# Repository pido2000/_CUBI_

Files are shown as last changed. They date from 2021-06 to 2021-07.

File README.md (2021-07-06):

### Description

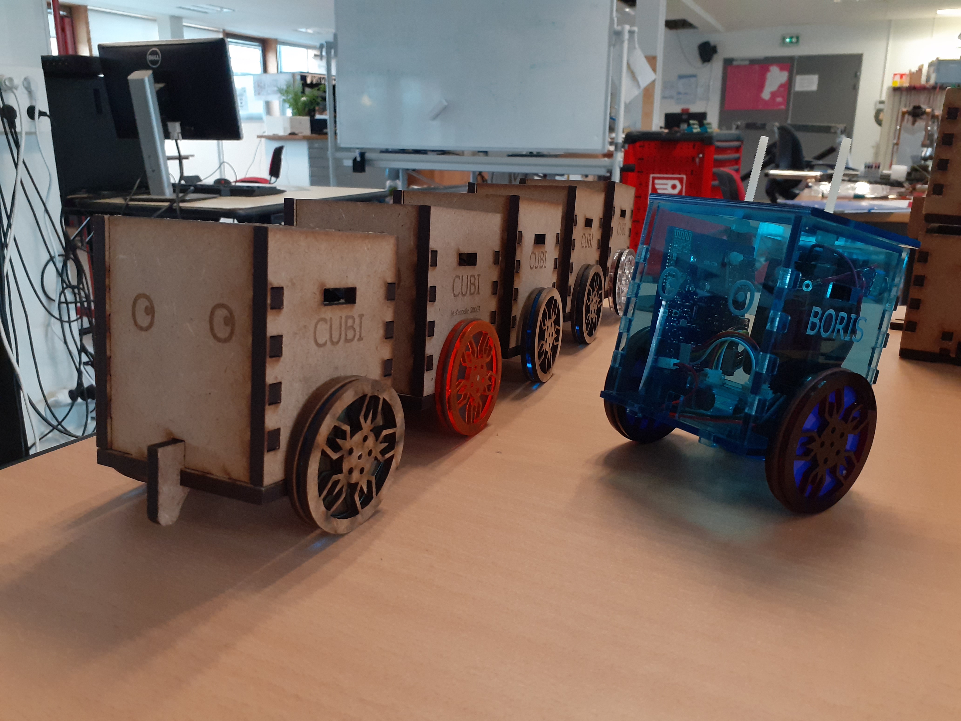
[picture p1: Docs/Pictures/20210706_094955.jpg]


Simple open source bluetooth controlled wheeled robot. Mechanical design, electronics and software designs available on this repo.
Remy F. used @Gregwar's Holo as a starting point.

The initial design is a cube like robot :

https://www.youtube.com/watch?v=2ZDV0_4vD0g

https://www.youtube.com/watch?v=TOusHRbKWQg

A second design was also made to play around cart-poling:

https://www.youtube.com/watch?v=Ubej95gH9Gs

TODO:

- Add Julien's O. designs and events

- Add Julien's A. and Jérémy's designs and event (cap science)

### Simulation
Some simulation stuff (simple kinematic control, inverted pendulum tests) is available in Python here :
https://bitbucket.org/RemiFabre/cubi/src/master/simulation/

0) Installation
You'll need Python (any version should work) and pygame
```
pip install pygame
```

1) Simple control of a wheeled robot (click around)
```
python main.py
```
https://www.youtube.com/watch?v=O8ZoUAvGYmE

2) Inverted pendulum (cart-pole) simulation
```
python cart_pole.py
```
https://www.youtube.com/watch?v=xhEcLnnj7fg

### How to make it work
You'll have to install the arm cross-compilation tools. On debian-like distributions,
you can get it with:

```
    sudo aptitude install build-essential git-core dfu-util openocd python \
        python-serial binutils-arm-none-eabi gcc-arm-none-eabi libstdc++-arm-none-eabi-newlib
```
If you're running an Ubuntu 14.04 or older, you might need to install the libstdc++-arm-none-eabi-newlib packet by hand. Download link :
http://ftp.de.debian.org/debian/pool/main/libs/libstdc++-arm-none-eabi/libstdc++-arm-none-eabi-newlib_4.8.3-9+4_all.deb

Command (if a conflict rises, you can add --force-overwrite to the following line):
```
	sudo dpkg -i libstdc++-arm-none-eabi-newlib_4.8.3-9+4_all.deb
```
Go to the `firmware/src` directory and edit the `Makefile` to set the appropriate
`BOARD` variable, targetting your servo.

You can then run:

```
make
```

Use an USB cable to connect your pc with the robot's board

```
make install
```
### Bluetooth

First you need to set the name and the pasword using a cable.

```
cu -l /dev/ttyACM0
btconf <name> <pswrd>
```

Then, you can control the robot without the need of a cable. The most straight-forward way is to download the "Metabot" app from Google Play. Once on the app you can scan for devices, find your robot and pair it with your phone.

If you want to pair your PC with your robot, one method is as follows (Ubuntu).

Uninstall modemmanager (not needed but causes some issues)

```
    sudo apt-get purge modemmanager
```

Scan for bluetooth devices and save the adress (e.g. 98:D3:37:90:ED:D6) of your robot. For example, we use blueman-manager :

```
    sudo apt-get install blueman
    sudo blueman-manager
```

Assign a serial port to the connection. You can do that on the graphical interface of blueman-manager but doing it directly with rfcomm seems more robust :

```
    sudo rfcomm bind /dev/rfcomm0 98:D3:37:90:ED:D6
```

Now you can access the remote terminal on the robot with :

```
    cu -l /dev/rfcomm0
```

You might have permission access issues. Make sure you're in the dialout group or go bonkers :

```
    sudo chmod 777 /dev/rfcomm0 && cu -l /dev/rfcomm0
```

### Electronics

A board was made with all integrated components in order to drop fabrication cost. 

Top

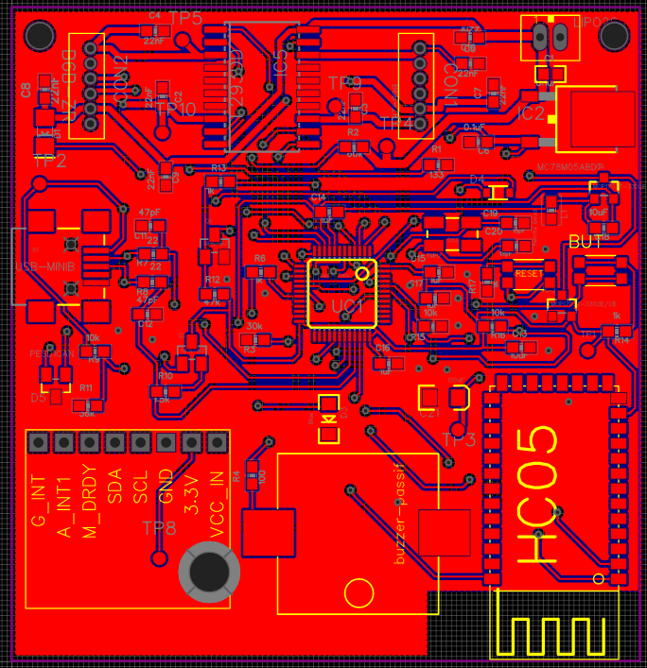
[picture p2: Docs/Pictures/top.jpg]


Bottom

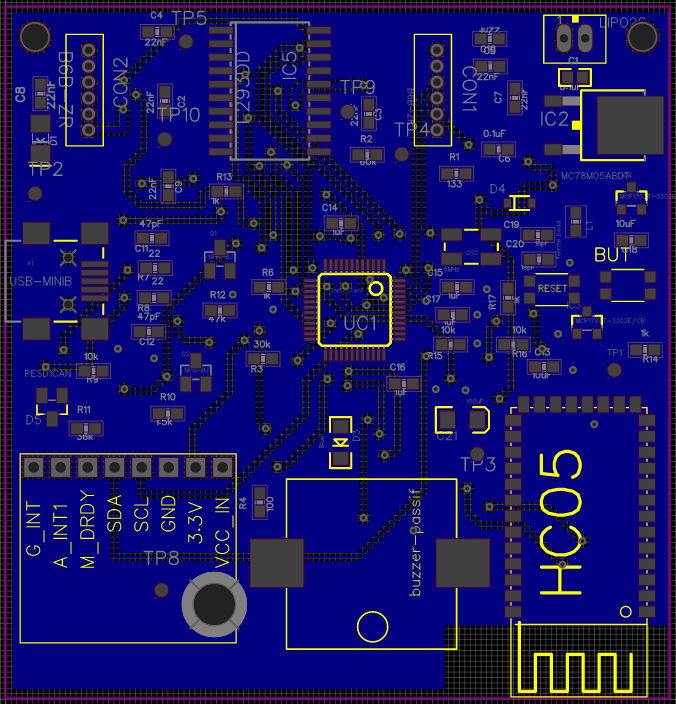
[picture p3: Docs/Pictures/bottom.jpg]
Cubi bottom


### Mecanics

Cubi's design is simple. It consist of a squared box. The majority was made in MDF.

Visual from Onshape
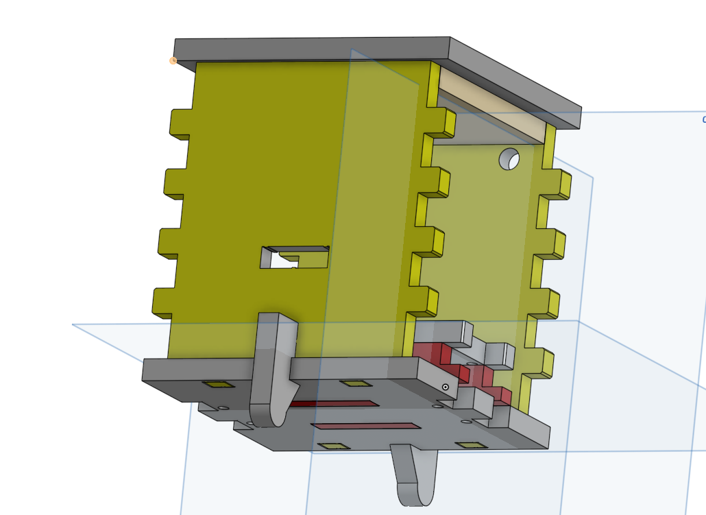
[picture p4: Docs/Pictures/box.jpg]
Cubi box


The design is transposed in the following svg file.
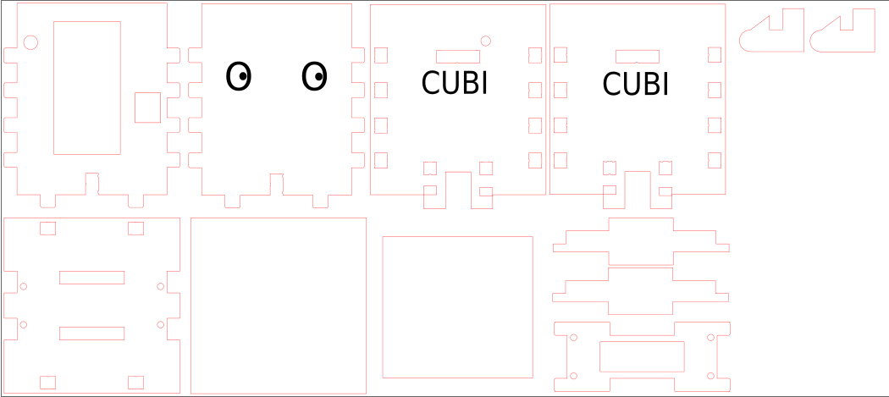
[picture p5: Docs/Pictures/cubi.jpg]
Cubi svg


We also enjoyed the look of PMMA.
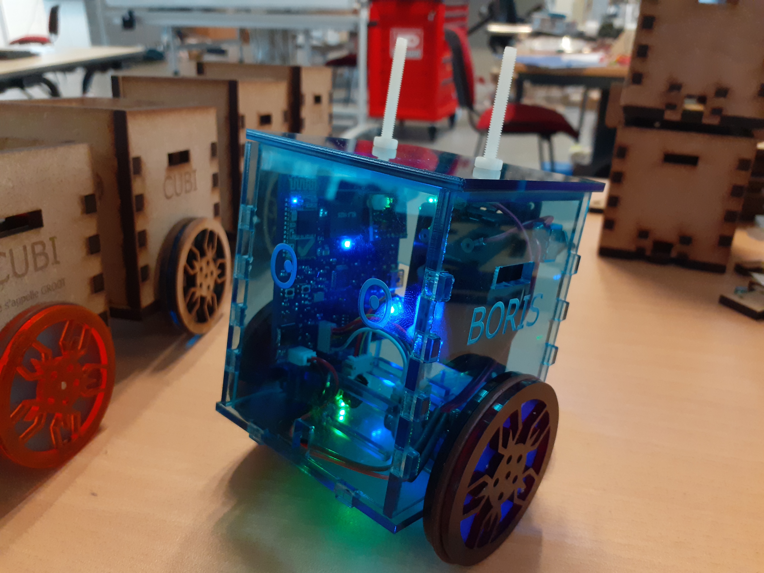
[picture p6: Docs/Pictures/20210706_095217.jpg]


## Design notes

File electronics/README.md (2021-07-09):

### cubi_board

Recent schematics and pcbs which integrates all the components on a standalone board in order to reduce manufacturing costs.
The board contains a µC (STM32F103CBT6), a hc-05 Bluetooth module, some voltage regulators... However, the GY-85 imu module is not integrated directly on the board.

All revisions used Eagle EDA except the last revision (rev. 8) designed on EasyEDA.

### maple-mini_board

Old schematics and pcbs using Maple Mini boards, mostly developed on Eagle EDA.

### remake_board

Recent tests made on CUBI electronic boards, developed on KiCad EDA.

The goal was to separate the motor driver and the 9V to 5V voltage regulator (the supply part) from the rest of components.
We wanted to add magnetic connectors (Pogo conn) to have a Plug And Play device.

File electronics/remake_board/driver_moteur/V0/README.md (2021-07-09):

### Description

Le projet "driver_moteur" est un prototype visant à séparer la carte électronique globale en 2 modules distincts pour faciliter le placement de cette carte à l'interieur du robot.
Pour une approche plus proche du Plug-And-Play, on voudrait aussi implanter des connecteurs magnétiques (Pogo pins) permettant de lier les 2 cartes facilement.

Un premier module s'occuperait de la gestion d'alimentation globale, avec le driver des moteurs et du régulateur 9V vers 5V.
Le deuxième module utiliserait le reste des composants traitant les données, avec le µC, le module Bluetooth, le buzzer et la centrale inertielle.

Ce projet est une piste d'amélioration (et d'optimisation) de la carte électronique.

### Inconvénient projet

Si l'on veut séparer la carte en 2 modules, cela implique un coût supplémentaire dû à la fabrication de 2 cartes distinctes + aux rajouts de connecteurs magnétiques liant celles-ci.

### Avantage projet

On peut connecter directement le module de gestion d'alim aux moteurs sans câbles et "plugger" l'autre module directement.
En effet, on peut difficilement créer une carte globale qui respecte les conditions de placement des connecteurs moteurs ET simplifie la mécanique du robot. 

### Notes à part

Nous n'avons créé qu'une seule version qui n'a pas encore été testée.
De plus, certaines soudures sont difficilement réalisables si l'on veut fabriquer le module soi-même.

Comme l'on possède 2 connecteurs Pogo de 8 broches, on a rajouté 4 pins disponibles pour commander des Leds supplémentaires.
Mais on peut tout à fait n'utiliser que 12 broches au total pour une version ultérieure du module.

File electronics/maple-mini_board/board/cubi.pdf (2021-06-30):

Pré-placement

On limite les boucles de courant fort. Dans ce cas, ca va être chiant, le connecteur du moteur étant juste complètement débile, la puissance passant sur les broches externe.
On peut quand même remarquer que M1 est gardé par une masse et M2 par VCC. On ajoute donc une capa de découplage entre Vcc et la masse, qui devra être placé au cul du connecteur.

On limite ainsi la casse : en HF, les fils de puissance M1 et M2 sont « blindé » par la masse.

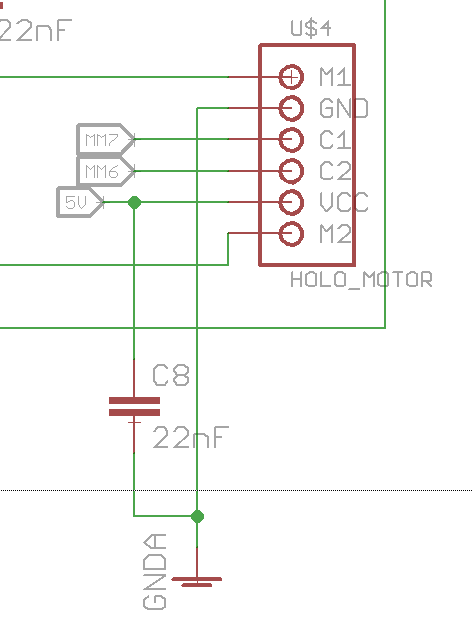
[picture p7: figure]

On place donc les connecteurs au plus court du pont. On limite ainsi les zones dangereuses (en jaune sur la figure). Dans ces zones, on fera particulièrement attention à ne pas fendre le plan de masse. Aucune piste sensible de doit traverser ces zones.

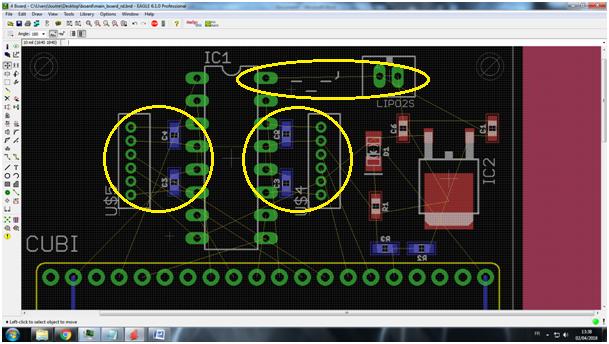
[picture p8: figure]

On tire les pistes fort courant en premier, pour voir à quoi on doit s’attendre. On passe ensuite quelques pistes de commande, pour avoir une idée du routage. On peut essayer de passer une alim au deux.

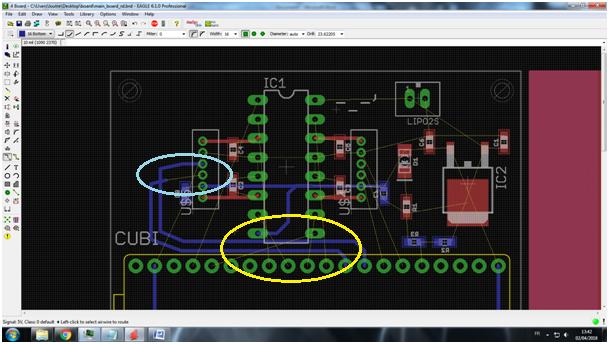
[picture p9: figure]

Premier constat : en bleu, les sorties codeurs croisent. Plus grave en jaune, là on sens que ca va être Beyrouth. Après étude du schéma, on voie que les fils non routé sont les PWM, donc des signaux rapide. Tant pis pour l’alim, elle dégage, on privilégie les signaux rapide au routage. On en profite pour réafecter les E/S pour que cela ne croise pas.

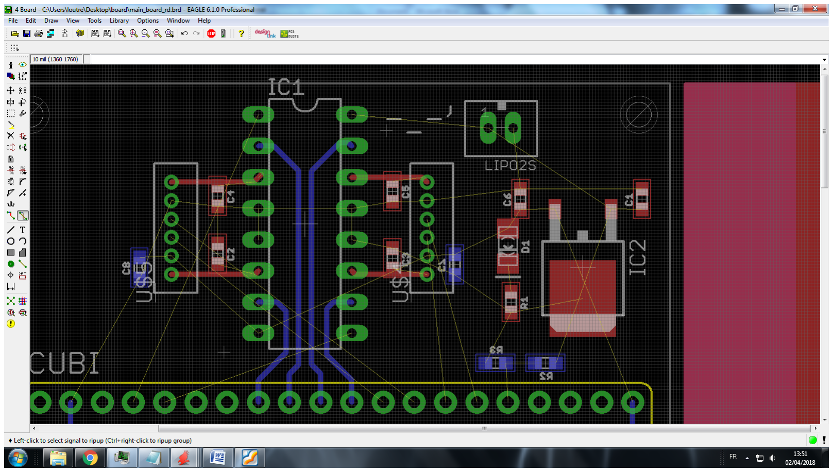
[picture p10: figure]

On passe toutes les PWM en BOTTOM : comme cela, le plan de masse en top fera écran (passer des pistes sous un composant de puissance, c’est dangereux, le composant rayonne, ce qui peut pourris les signaux)

On reprend le routage des codeurs :

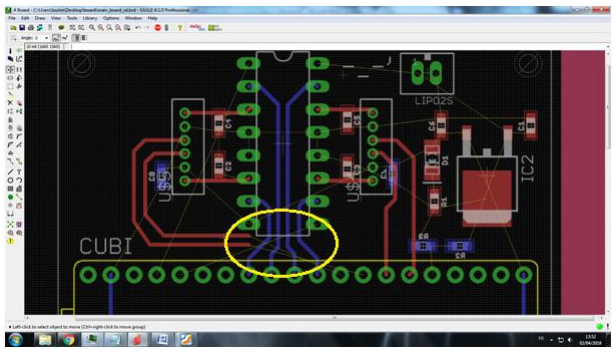
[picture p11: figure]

En jaune, c’est la seconde guerre du Golf. On doit croiser les codeurs avec les PWM, donc fendre le plan de masse. Or, pour rappel, règle N°1 en routage : ON NE FEND JAMAIS UN PLAN DE MASSE (Bordel). Bon, là on est en deux couches donc, on se détend.
Règle N°2 du routage : en deux couches, si on doit croiser des pistes, on se réfère à la règle N°1.

Dans notre cas, on fait le tour par le haut.

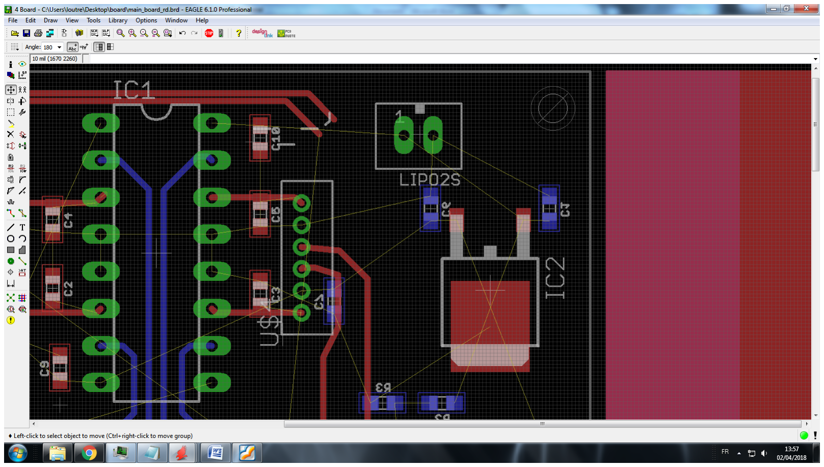
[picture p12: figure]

Bon c’est pas top. Mais a défaut… on va croiser l’alim mais avec les capas de découplages ca devrait aller (Les capas sur VCC1 et VCC2 ont été ajouté, elles avaient été oublié)

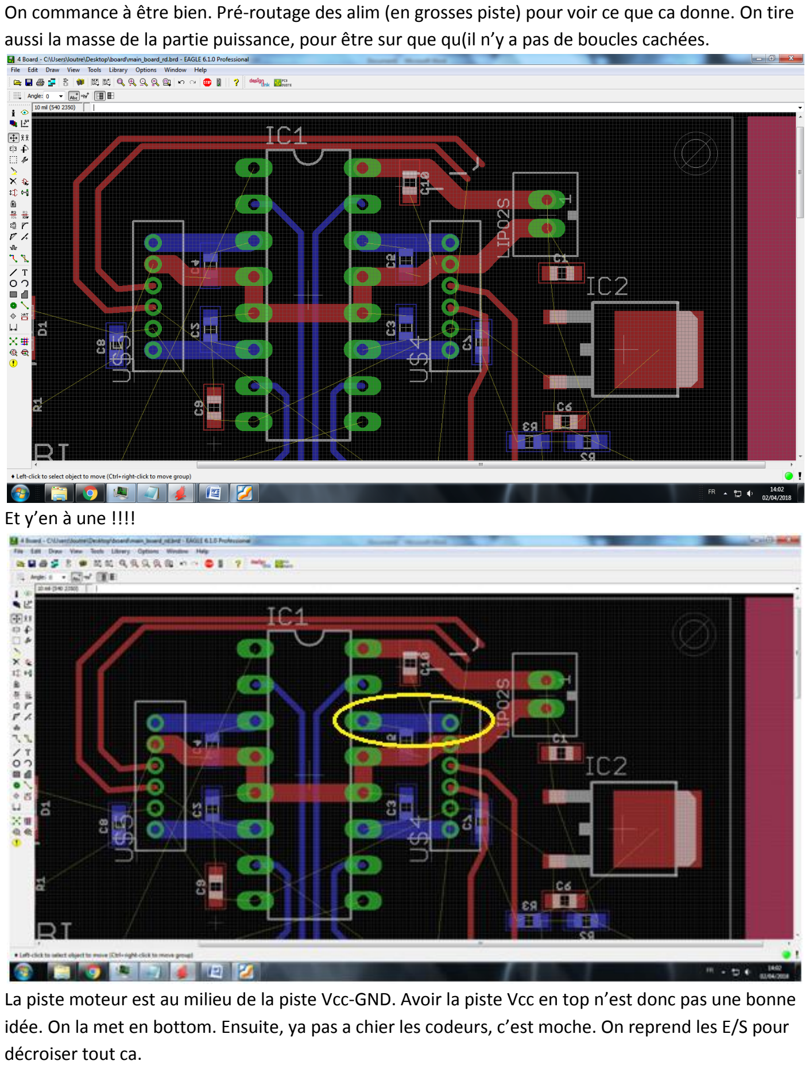
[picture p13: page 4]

On commance à être bien. Pré-routage des alim (en grosses piste) pour voir ce que ca donne. On tire aussi la masse de la partie puissance, pour être sur que qu(il n’y a pas de boucles cachées.

Et y’en à une !!!!

La piste moteur est au milieu de la piste Vcc-GND. Avoir la piste Vcc en top n’est donc pas une bonne idée. On la met en bottom. Ensuite, ya pas a chier les codeurs, c’est moche. On reprend les E/S pour décroiser tout ca.

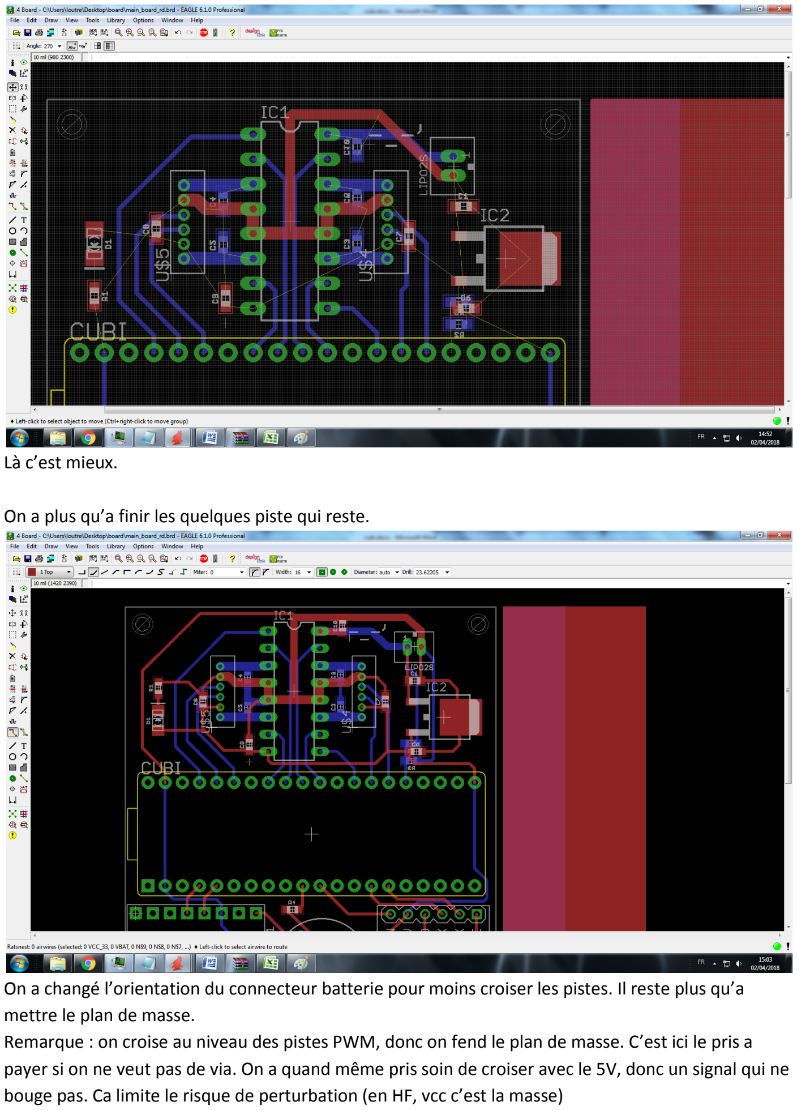
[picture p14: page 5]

Là c’est mieux.

On a plus qu’a finir les quelques piste qui reste.

On a changé l’orientation du connecteur batterie pour moins croiser les pistes. Il reste plus qu’a mettre le plan de masse.
Remarque : on croise au niveau des pistes PWM, donc on fend le plan de masse. C’est ici le pris a payer si on ne veut pas de via. On a quand même pris soin de croiser avec le 5V, donc un signal qui ne bouge pas. Ca limite le risque de perturbation (en HF, vcc c’est la masse)

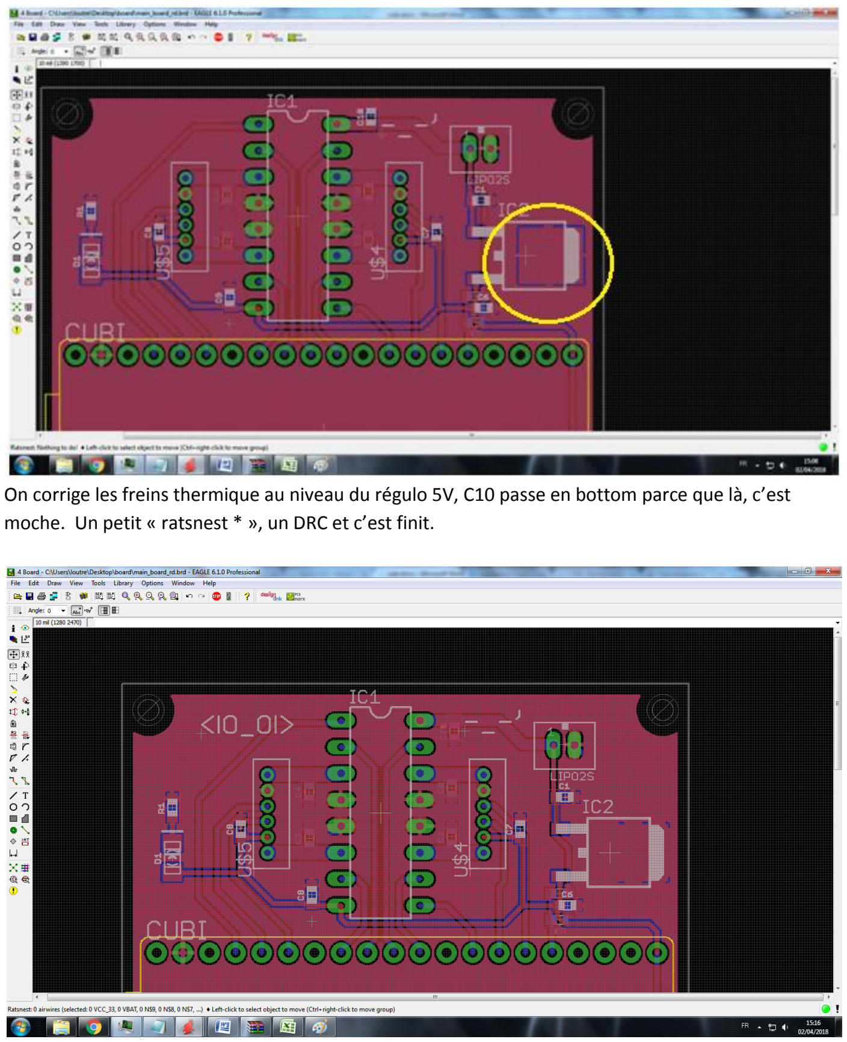
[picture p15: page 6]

On corrige les freins thermique au niveau du régulo 5V, C10 passe en bottom parce que là, c’est moche. Un petit « ratsnest * », un DRC et c’est finit.

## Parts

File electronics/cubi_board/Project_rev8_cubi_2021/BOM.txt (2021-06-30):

Partlist exported from C:/Users/elkat/Documents/EAGLE/projects/electronics/rev7/rev7.sch at 24/09/2019 17:15

Part   Value               Device                     Package               Description                               FARNELL      MF MPN OC_FARNELL PROD_ID   TP_SIGNAL_NAME VALUE
BUT    KMR211GLFS          BUTTON-KMR241GLFS          PUSHBUTTON-KMR241GLFS                                                                                                        
C1     0.1uF               0.1UF-0603-25V-(+80/-20%)  0603                  0.1µF ceramic capacitors                                                 CAP-00810                0.1uF
C2     22nF                22NF/22,000PF-0603-50V-10% 0603                  0.022uF/22nF/22,000pF ceramic capacitors                                 CAP-07885                22nF 
C3     22nF                22NF/22,000PF-0603-50V-10% 0603                  0.022uF/22nF/22,000pF ceramic capacitors                                 CAP-07885                22nF 
C4     22nF                22NF/22,000PF-0603-50V-10% 0603                  0.022uF/22nF/22,000pF ceramic capacitors                                 CAP-07885                22nF 
C5     22nF                22NF/22,000PF-0603-50V-10% 0603                  0.022uF/22nF/22,000pF ceramic capacitors                                 CAP-07885                22nF 
C6     0.1uF               0.1UF-0603-25V-(+80/-20%)  0603                  0.1µF ceramic capacitors                                                 CAP-00810                0.1uF
C7     22nF                22NF/22,000PF-0603-50V-10% 0603                  0.022uF/22nF/22,000pF ceramic capacitors                                 CAP-07885                22nF 
C8     22nF                22NF/22,000PF-0603-50V-10% 0603                  0.022uF/22nF/22,000pF ceramic capacitors                                 CAP-07885                22nF 
C9     22nF                22NF/22,000PF-0603-50V-10% 0603                  0.022uF/22nF/22,000pF ceramic capacitors                                 CAP-07885                22nF 
C10    22nF                22NF/22,000PF-0603-50V-10% 0603                  0.022uF/22nF/22,000pF ceramic capacitors                                 CAP-07885                22nF 
C11    47pF                0.1UF-0603-25V-(+80/-20%)  0603                  0.1µF ceramic capacitors                                                 CAP-00810                0.1uF
C12    47pF                0.1UF-0603-25V-(+80/-20%)  0603                  0.1µF ceramic capacitors                                                 CAP-00810                0.1uF
C13    10uF                0.1UF-0603-25V-(+80/-20%)  0603                  0.1µF ceramic capacitors                                                 CAP-00810                0.1uF
C14    1uF                 0.1UF-0603-25V-(+80/-20%)  0603                  0.1µF ceramic capacitors                                                 CAP-00810                0.1uF
C15    1uF                 0.1UF-0603-25V-(+80/-20%)  0603                  0.1µF ceramic capacitors                                                 CAP-00810                0.1uF
C16    1uF                 0.1UF-0603-25V-(+80/-20%)  0603                  0.1µF ceramic capacitors                                                 CAP-00810                0.1uF
C17    1uF                 0.1UF-0603-25V-(+80/-20%)  0603                  0.1µF ceramic capacitors                                                 CAP-00810                0.1uF
C18    10uF                0.1UF-0603-25V-(+80/-20%)  0603                  0.1µF ceramic capacitors                                                 CAP-00810                0.1uF
C19    18pF                0.1UF-0603-25V-(+80/-20%)  0603                  0.1µF ceramic capacitors                                                 CAP-00810                0.1uF
C20    18pF                0.1UF-0603-25V-(+80/-20%)  0603                  0.1µF ceramic capacitors                                                 CAP-00810                0.1uF
C21    100uF               CAP_POL1206                EIA3216               Capacitor Polarized                                                                                    
CON1   B6B-ZR              B6B-ZR                     B6B-ZR                JST-ZH Connector                                                                                       
CON2   B6B-ZR              B6B-ZR                     B6B-ZR                JST-ZH Connector                                                                                       
D1                         LED-FKIT-1206              FKIT-LED-1206         LED (Generic)                                                                                          
D3     Blue                LED1206                    LED-1206              LEDs                                                                                                   
D4                         DIODESOD                   SOD-323               Diode                                                                                                  
D5     PESD1CAN            PESD1CAN                   SOT23                 CAN bus ESD protection diode                                                                           
IC2    MC78M05ABDT         MC78M05ABDT                DPACK_3               500 mA Positive Voltage Regulators                                                                     
IC3    MCP1703T-3302E/CB   MCP1700T                   SOT23                                                                                                                        
IC4    MCP1703T-3302E/CB   MCP1700T                   SOT23                                                                                                                        
IC5    L293DD              L293DD                     SO20                  PUSH-PULL FOUR CHANNEL DRIVER WITH DIODES                     unknown                                  
L1     ferrite bead        INDUCTOR0603               0603                  Inductors                                                                                              
LIPO2S JST-PH_2-PIN_HEADER JST-PH_2-PIN_HEADER        JST_B2B-PH_HEADER     2-pin JST PH Shrouded Header, top entry                                                                
OSC    8MHz                CRYSTAL5X3                 CRYSTAL-SMD-5X3       Crystals                                                                                               
Q1     NPN-BJT             TRANSISTOR_NPNSOT23        SOT23                 Transistor NPN                                                                                         
Q2     NPN-BJT             TRANSISTOR_NPNSOT23        SOT23                 Transistor NPN                                                                                         
R1     133                 0.27OHM-0603-1/10W-1%      0603                  0.27Ω resistor                                                           RES-08787                0.27 
R2     60k                 0.27OHM-0603-1/10W-1%      0603                  0.27Ω resistor                                                           RES-08787                0.27 
R3     30k                 0.27OHM-0603-1/10W-1%      0603                  0.27Ω resistor                                                           RES-08787                0.27 
R4     100                 0.27OHM-0603-1/10W-1%      0603                  0.27Ω resistor                                                           RES-08787                0.27 
R6     1k                  0.27OHM-0603-1/10W-1%      0603                  0.27Ω resistor                                                           RES-08787                0.27 
R7     22                  0.27OHM-0603-1/10W-1%      0603                  0.27Ω resistor                                                           RES-08787                0.27 
R8     22                  0.27OHM-0603-1/10W-1%      0603                  0.27Ω resistor                                                           RES-08787                0.27 
R9     10k                 0.27OHM-0603-1/10W-1%      0603                  0.27Ω resistor                                                           RES-08787                0.27 
R10    1.5k                0.27OHM-0603-1/10W-1%      0603                  0.27Ω resistor                                                           RES-08787                0.27 
R11    36k                 0.27OHM-0603-1/10W-1%      0603                  0.27Ω resistor                                                           RES-08787                0.27 
R12    47k                 0.27OHM-0603-1/10W-1%      0603                  0.27Ω resistor                                                           RES-08787                0.27 
R13    1k                  0.27OHM-0603-1/10W-1%      0603                  0.27Ω resistor                                                           RES-08787                0.27 
R14    1k                  0.27OHM-0603-1/10W-1%      0603                  0.27Ω resistor                                                           RES-08787                0.27 
R15    10k                 0.27OHM-0603-1/10W-1%      0603                  0.27Ω resistor                                                           RES-08787                0.27 
R16    10k                 0.27OHM-0603-1/10W-1%      0603                  0.27Ω resistor                                                           RES-08787                0.27 
R17    1k                  0.27OHM-0603-1/10W-1%      0603                  0.27Ω resistor                                                           RES-08787                0.27 
RESET  KMR211GLFS          BUTTON-KMR241GLFS          PUSHBUTTON-KMR241GLFS                                                                                                        
TP1    PTR1B1,27           PTR1B1,27                  B1,27                 TEST PIN                                                                                               
TP2    PTR1B1,27           PTR1B1,27                  B1,27                 TEST PIN                                                                                               
TP3    PTR1B1,27           PTR1B1,27                  B1,27                 TEST PIN                                                                                               
TP4    PTR1B1,27           PTR1B1,27                  B1,27                 TEST PIN                                                                                               
TP5    PTR1B1,27           PTR1B1,27                  B1,27                 TEST PIN                                                                                               
TP8    PTR1B1,27           PTR1B1,27                  B1,27                 TEST PIN                                                                                               
TP9    PTR1B1,27           PTR1B1,27                  B1,27                 TEST PIN                                                                                               
TP10   PTR1B1,27           PTR1B1,27                  B1,27                 TEST PIN                                                                                               
U$1    BUZZER-PASSIF       BUZZER-PASSIF              BUZZER-PASSIF         buzzer-passif                                                                                          
U$4    HC05                HC05                       HC-05                                                           MODULE HC-05                                                 
U$6    GY-85               GY-85                      GY-85                                                                                                                        
UC1    STM32F103CBT6       STM32F103CB                LQFP48                                                                                                                       
X1     USB-MINIB           USBSMD                     USB-MINIB             USB Connectors

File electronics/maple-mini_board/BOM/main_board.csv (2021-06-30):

Part | Value | Device | Package | Description | MF | MPN | OC_FARNELL | OC_NEWARK | PROD_ID | VALUE | Link | bundle_number | bundle_price | Unit price
C1 | 0.1uF | 0.1UF-0603-25V-(+80/-20%) | 603 | 0.1µF ceramic capacitors |  |  |  |  | CAP-00810 | 0.1uF | https://fr.aliexpress.com/item/Durable-in-Use-0603-SMD-Chip-Capacitors-0-5pF-2-2uF-90Valuesx50-Sample-Book-Assortment-Kit/32721099737.html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 |  |  | 0.01
C2 | 22nF | 22NF/22,000PF-0603-50V-10% | 603 | 0.022uF/22nF/22,000pF ceramic capacitors |  |  |  |  | CAP-07885 | 22nF |  |  |  | 0.01
C3 | 22nF | 22NF/22,000PF-0603-50V-10% | 603 | 0.022uF/22nF/22,000pF ceramic capacitors |  |  |  |  | CAP-07885 | 22nF |  |  |  | 0.01
C4 | 22nF | 22NF/22,000PF-0603-50V-10% | 603 | 0.022uF/22nF/22,000pF ceramic capacitors |  |  |  |  | CAP-07885 | 22nF |  |  |  | 0.01
C5 | 22nF | 22NF/22,000PF-0603-50V-10% | 603 | 0.022uF/22nF/22,000pF ceramic capacitors |  |  |  |  | CAP-07885 | 22nF |  |  |  | 0.01
C6 | 0.1uF | 0.1UF-0603-25V-(+80/-20%) | 603 | 0.1µF ceramic capacitors |  |  |  |  | CAP-00810 | 0.1uF |  |  |  | 0.01
D1 |  | LED-FKIT-1206 | FKIT-LED-1206 | LED (Generic) |  |  |  |  |  |  | https://fr.aliexpress.com/item/1206-SMD-LED-SMD-LED-blue-green-and-white-bag-sample-pack-5-colors-each-20/32289160842.html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 |  |  | 0.01
D2 |  | LED-FKIT-1206 | FKIT-LED-1206 | LED (Generic) |  |  |  |  |  |  |  |  |  | 0.01
IC1 | L293D | L293D | DIL16 | PUSH-PULL 4 CHANNEL DRIVER |  | L293D | 9589619 | 56P8249 |  |  | https://fr.aliexpress.com/item/50-PCS-L293D-DIP16-L293-DIP-nouveau-original-livraison-gratuite/32861102517.html | 50 | 11.01 | 0.2202
IC2 | MC78M05ABDT | MC78M05ABDT | DPACK_3 | 500 mA Positive Voltage Regulators |  |  |  |  |  |  | https://fr.aliexpress.com/item/Free-shipping-20pcs-New-78M05-TO252-7805-750mA/32617637330.html | 30 | 1.03 | 0.0343333333
LIPO2S | JST-PH_2-PIN_HEADER | JST-PH_2-PIN_HEADER | JST_B2B-PH_HEADER | 2-pin JST PH Shrouded Header, top entry
R1 | 133 | 0.27OHM-0603-1/10W-1% | 603 | resistor |  |  |  |  | RES-08787 | 0.27 | https://fr.aliexpress.com/item/0603-SMD-Resistor-Kit-Assorted-Kit-1-chip-resistor-element-170-values-50pcs/32546720452.html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
R2 | 60k | 0.27OHM-0603-1/10W-1% | 603 | resistor |  |  |  |  | RES-08787 | 0.27 |  |  |  | 0.01
R3 | 30k | 0.27OHM-0603-1/10W-1% | 603 | resistor |  |  |  |  | RES-08787 | 0.27 |  |  |  | 0.01
R4 | 100 | 0.27OHM-0603-1/10W-1% | 603 | resistor |  |  |  |  | RES-08787 | 0.27 |  |  |  | 0.01
R5 | 133 | 0.27OHM-0603-1/10W-1% | 603 | resistor |  |  |  |  | RES-08787 | 0.27 |  |  |  | 0.01
SG1 | F/CM12P | F/CM12P | F/CM12P | BUZZER Source: Buerklin |  |  | unknown | unknown |  |  | https://fr.aliexpress.com/item/5PCS-Lot-Passive-Buzzer-AC-12MM-8-5MM-12085-16R-Resistance-3V-5V-9V-12V-In/32503620431.html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 | 10 | 0.95 | 0.095
U$1 | MAPLEMINI | MAPLEMINI | 20-DIP |  |  |  |  |  |  |  | https://fr.aliexpress.com/item/5PCS-LOT-leaflabs-Leaf-maple-mini-ARM-STM32-compatibility/1400682373.html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 | 5 | 14.43 | 2.886
U$3 | WIRELESS-BLUETOOTH-HC-05 | WIRELESS-BLUETOOTH-HC-05 | WIRELESS-BLUETOOTH-HC-05 | Bluetooth Transceiver Module based on HC-05 board |  |  |  |  |  |  | https://fr.aliexpress.com/item/HC05-HC-05-master-slave-6pin-JY-MCU-anti-reverse-integrated-Bluetooth-serial-pass-through-module/32272705461.html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 | 5 | 13 | 2.6
U$4 | HOLO_MOTOR | HOLO_MOTOR | HOLO_MOTOR |  |  |  |  |  |  |  | https://fr.aliexpress.com/item/5PCS-Well-made-GA12-N20-dc-gear-motor-with-encoder-speed-velocity-measurement-6V-500rpm-FOR/32615345501.html | 5 | 39.3 | 7.86
U$5 | HOLO_MOTOR | HOLO_MOTOR | HOLO_MOTOR |  |  |  |  |  |  |  |  |  |  | 7.86
U$6 | GY-85 | GY-85 | GY-85 |  |  |  |  |  |  |  | https://fr.aliexpress.com/item/GY-85-BMP085-Sensor-Modules-9-Axis-Sensor-Module-ITG3205-ADXL345-HMC5883L-6DOF-9DOF-IMU-Sensor/2024503421.html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 | 1 | 8.17 | 8.17
 |  | 9V Battery Snap connector |  |  |  |  |  |  |  |  | https://fr.aliexpress.com/item/10pcs-9V-Battery-Snap-Connector-clip-Lead-Wires-holder/32825539506.html | 10 | 0.82 | 0.082
 |  | 9V rechargeable Battery |  |  |  |  |  |  |  |  | https://fr.aliexpress.com/item/1pcs-ZNTER-9V-400mAh-lithium-li-po-li-ion-rechargeable-battery-micro-usb-cable-for-charging/32805810958.html | 2 | 14.14 | 7.07
 |  |  |  |  |  |  |  |  |  |  |  |  | Total | 36.9975333333

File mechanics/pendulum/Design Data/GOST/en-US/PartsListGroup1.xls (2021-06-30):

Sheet: Лист 1
Инв. № подл |  |  |  | Подп. и дата | Взам. инв. № | Инв. № дубл. |  |  | Подп. и дата
Формат | Зона | Поз. | Обозначение |  |  |  | Наименование |  |  |  |  |  | Кол. на исполнение
 |  |  |  |  |  |  |  |  |  |  |  | Лит.
 |  |  |  |  |  |  |  |  |  |  |  | Код
 |  |  |  |  |  |  |  | Изм. | Лист | № докум | Подпись |  | Дата
 |  |  |  |  |  |  |  | Разраб.
 |  |  |  |  |  |  |  | Пров.
 |  |  |  |  |  |  |  | Н.контр
 |  |  |  |  |  |  |  | Утв.
 |  |  |  |  |  |  |  |  |  |  |  |  |  | Копировал

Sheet: Лист 2
Инв. № подл |  |  |  | Подп. и дата | Взам. инв. № | Инв. № дубл. |  |  | Подп. и дата
Формат | Зона | Поз. | Обозначение |  |  |  | Наименование |  |  |  |  | Кол. на исполнение
 |  |  |  |  |  |  |  | Изм. | Лист | № докум. | Подп. | Дата
 |  |  |  |  |  |  |  |  |  |  |  |  | Копировал
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

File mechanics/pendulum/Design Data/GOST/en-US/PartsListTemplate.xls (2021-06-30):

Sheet: Лист 1
 | Формат | Зона |  | Поз. |  | Обозначение |  |  |  | Наименование |  |  |  | Кол. | Приме-чание
Подп. и дата
Инв. № дубл.
Взам. инв. №
Подп. и дата
 | Изм. |  | Лист |  | № докум |  | Подпись | Дата
Инв. № подл | Разраб. |  |  |  |  |  |  |  |  |  | Литера |  | Лист |  |  | Листов
 | Пров.
 | Н.контр
 | Утв.
 |  |  |  |  |  |  |  |  | Копировал |  |  | Формат А4

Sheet: Лист 2
 | Формат | Зона |  | Поз. |  | Обозначение |  |  |  | Наименование |  | Кол. | Приме-чание
Подп. и дата
Инв. № дубл.
Взам. инв. №
Подп. и дата
Инв. № подл
 | Изм. |  | Лист |  | № докум. |  | Подп. |  | Дата
 |  |  |  |  |  |  |  | Копировал |  |  | Формат А4
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

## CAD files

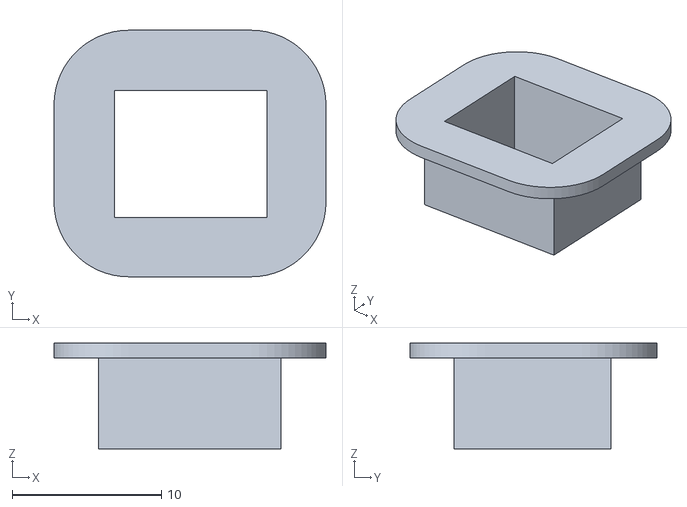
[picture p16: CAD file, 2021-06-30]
mechanics/cache_prise.stl
18.2 x 16.5 x 7.07

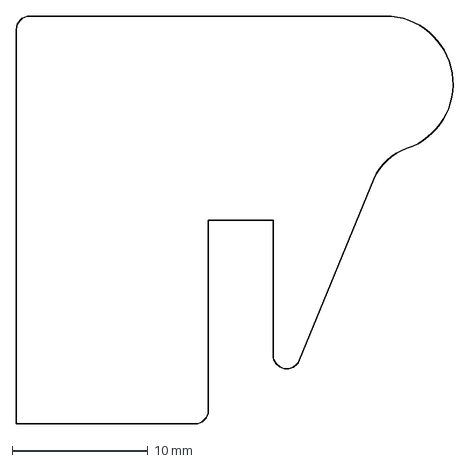
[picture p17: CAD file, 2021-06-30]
mechanics/export/V1-bis/nez.dxf
32.4 x 30.0 mm

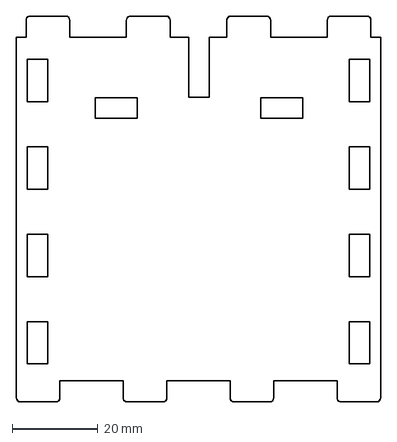
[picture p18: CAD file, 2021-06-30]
mechanics/export/V2/devant.dxf
85.0 x 90.0 mm

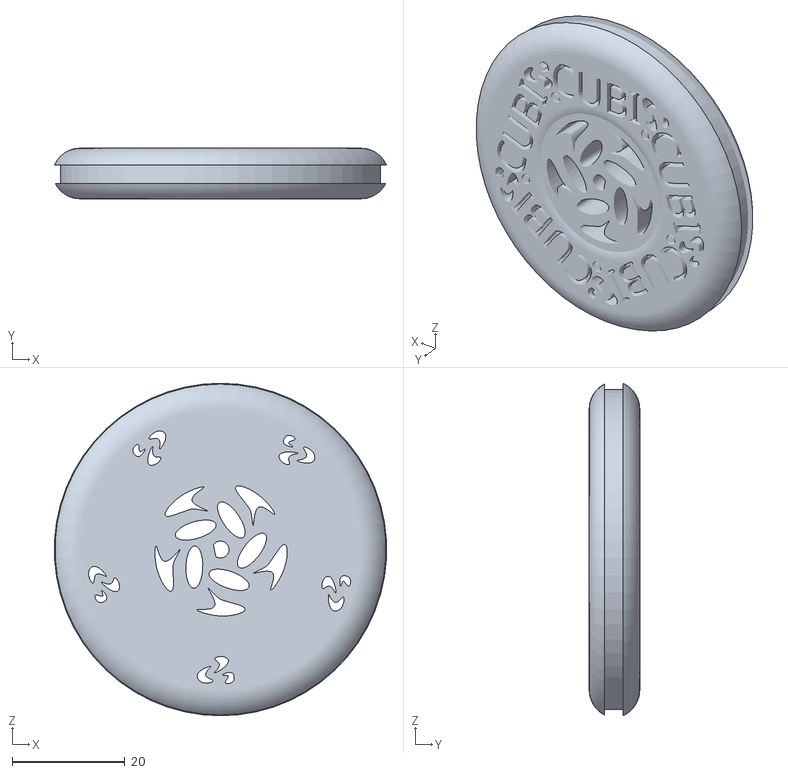
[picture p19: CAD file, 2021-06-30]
mechanics/cubi_wheel.stl
59.0 x 9.00 x 59.1

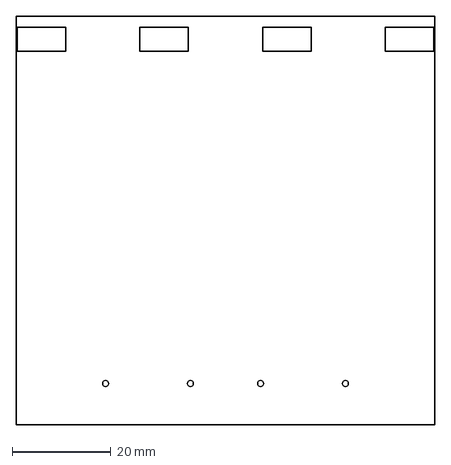
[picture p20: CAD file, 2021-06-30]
mechanics/export/V1-bis/tete.dxf
85.0 x 82.9 mm

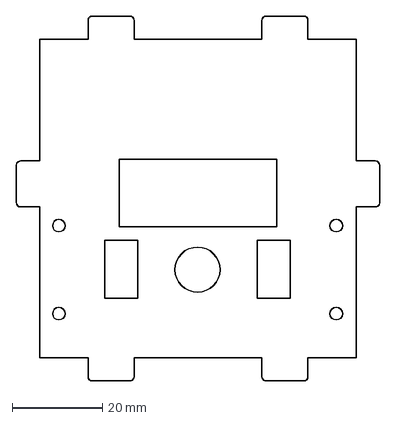
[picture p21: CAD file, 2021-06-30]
mechanics/export/V2/etage.dxf
80.6 x 80.9 mm

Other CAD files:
mechanics/new_tiny/cubi.dwg
mechanics/new_tiny/modules/attrape_ball.dwg
mechanics/pendulum/Templates/English/am_ansi.dwg
mechanics/pendulum/Templates/Metric/am_iso.dwg
mechanics/pendulum/Templates/Standard.dwg
mechanics/tiny/Templates/English/am_ansi.dwg
mechanics/tiny/Templates/Metric/GB.dwg
mechanics/tiny/Templates/Standard.dwg
mechanics/new_tiny/modules/for_metabois.dwg
mechanics/pendulum/Templates/English/ANSI (in).dwg
mechanics/pendulum/Templates/Metric/GB.dwg
mechanics/tiny/Templates/English/ANSI (in).dwg
mechanics/ON-OFF_v2.stl
mechanics/Old_meca/OldVersions/base2.0002.ipt
mechanics/Old_meca/OldVersions/capot.0002.ipt
mechanics/Old_meca/OldVersions/motorbox_bottom.0012.ipt
mechanics/Old_meca/OldVersions/wheel_to_motor.0012.ipt
mechanics/Old_meca/base.iam
mechanics/Old_meca/base.ipt
mechanics/Old_meca/battery.ipt
mechanics/Old_meca/board_rev0.ipt
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

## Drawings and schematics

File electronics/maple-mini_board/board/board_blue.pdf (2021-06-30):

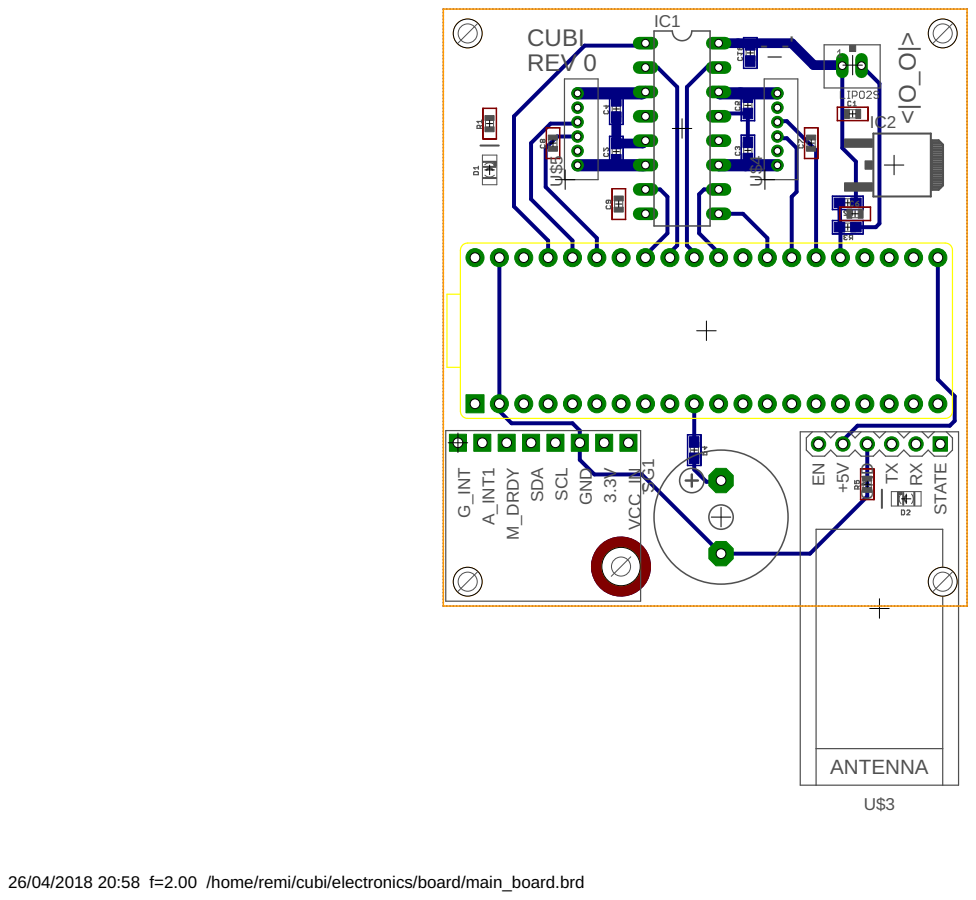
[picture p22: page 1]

26/04/2018 20:58 f=2.00 /home/remi/cubi/electronics/board/main_board.brd

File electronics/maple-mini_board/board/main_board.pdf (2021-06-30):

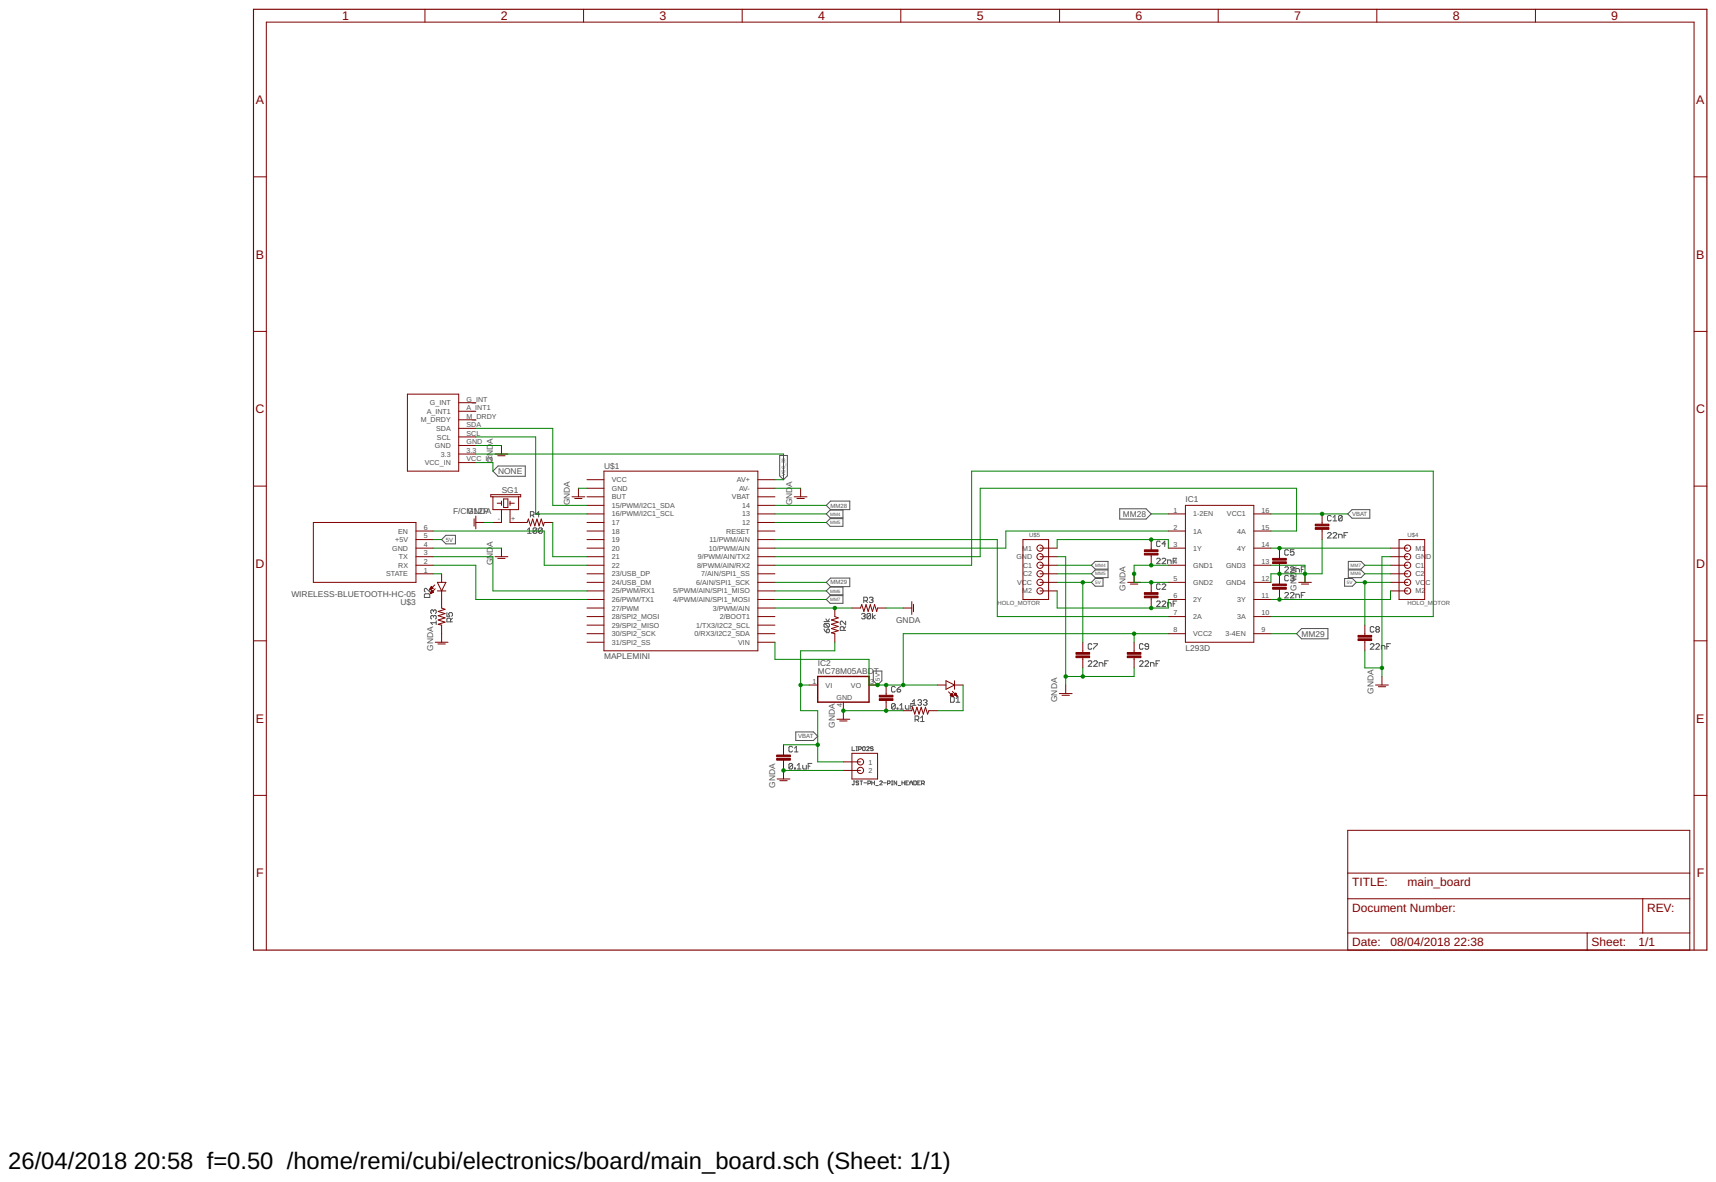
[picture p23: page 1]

11/PWM/AIN
10/PWM/AIN
9/PWM/AIN/TX2
8/PWM/AIN/RX2
7/AIN/SPI1_SS
6/AIN/SPI1_SCK
5/PWM/AIN/SPI1_MISO
4/PWM/AIN/SPI1_MOSI 3/PWM/AIN

26/04/2018 20:58 f=0.50 /home/remi/cubi/electronics/board/main_board.sch (Sheet: 1/1)

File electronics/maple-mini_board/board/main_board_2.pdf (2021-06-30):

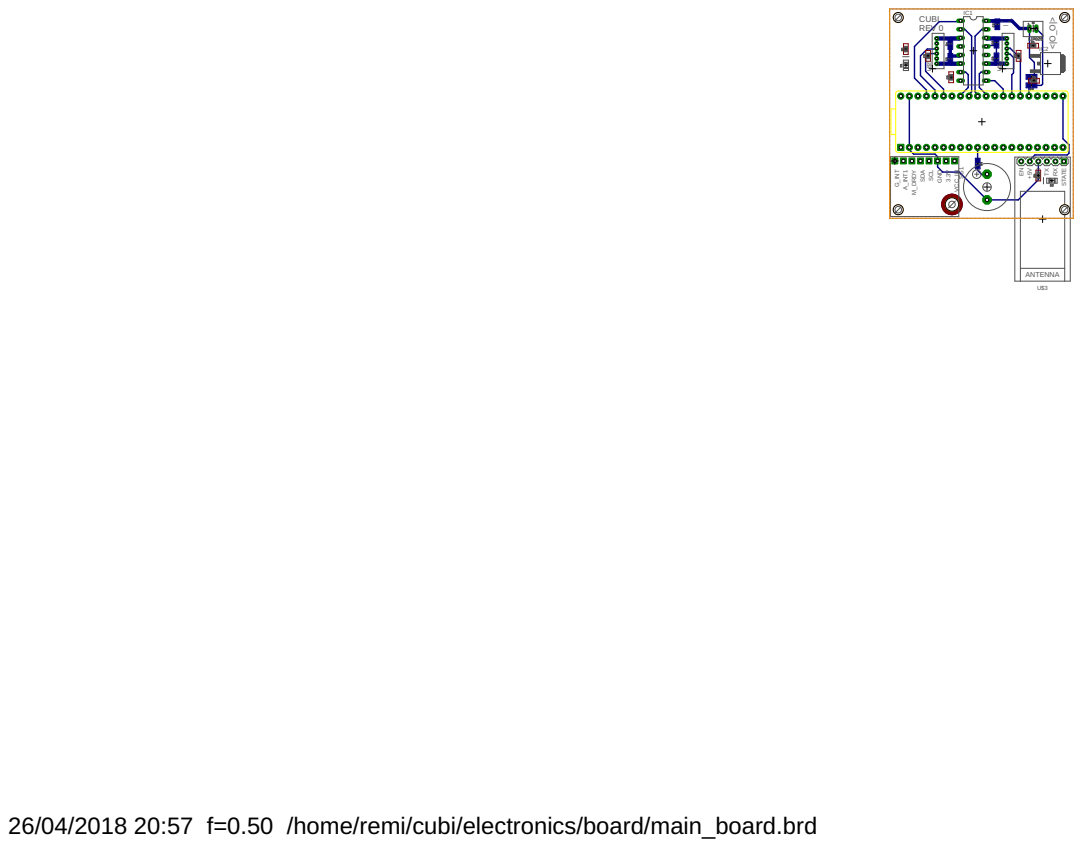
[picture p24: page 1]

26/04/2018 20:57 f=0.50 /home/remi/cubi/electronics/board/main_board.brd

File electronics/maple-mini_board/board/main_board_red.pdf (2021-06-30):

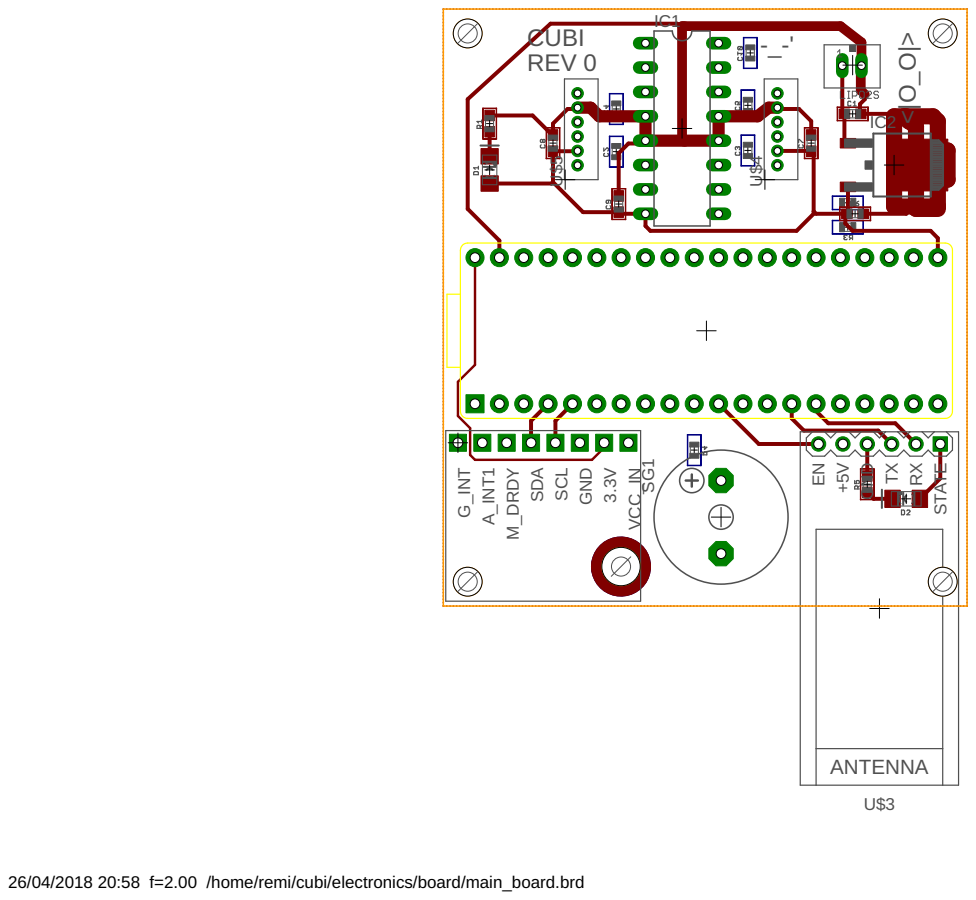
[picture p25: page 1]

26/04/2018 20:58 f=2.00 /home/remi/cubi/electronics/board/main_board.brd

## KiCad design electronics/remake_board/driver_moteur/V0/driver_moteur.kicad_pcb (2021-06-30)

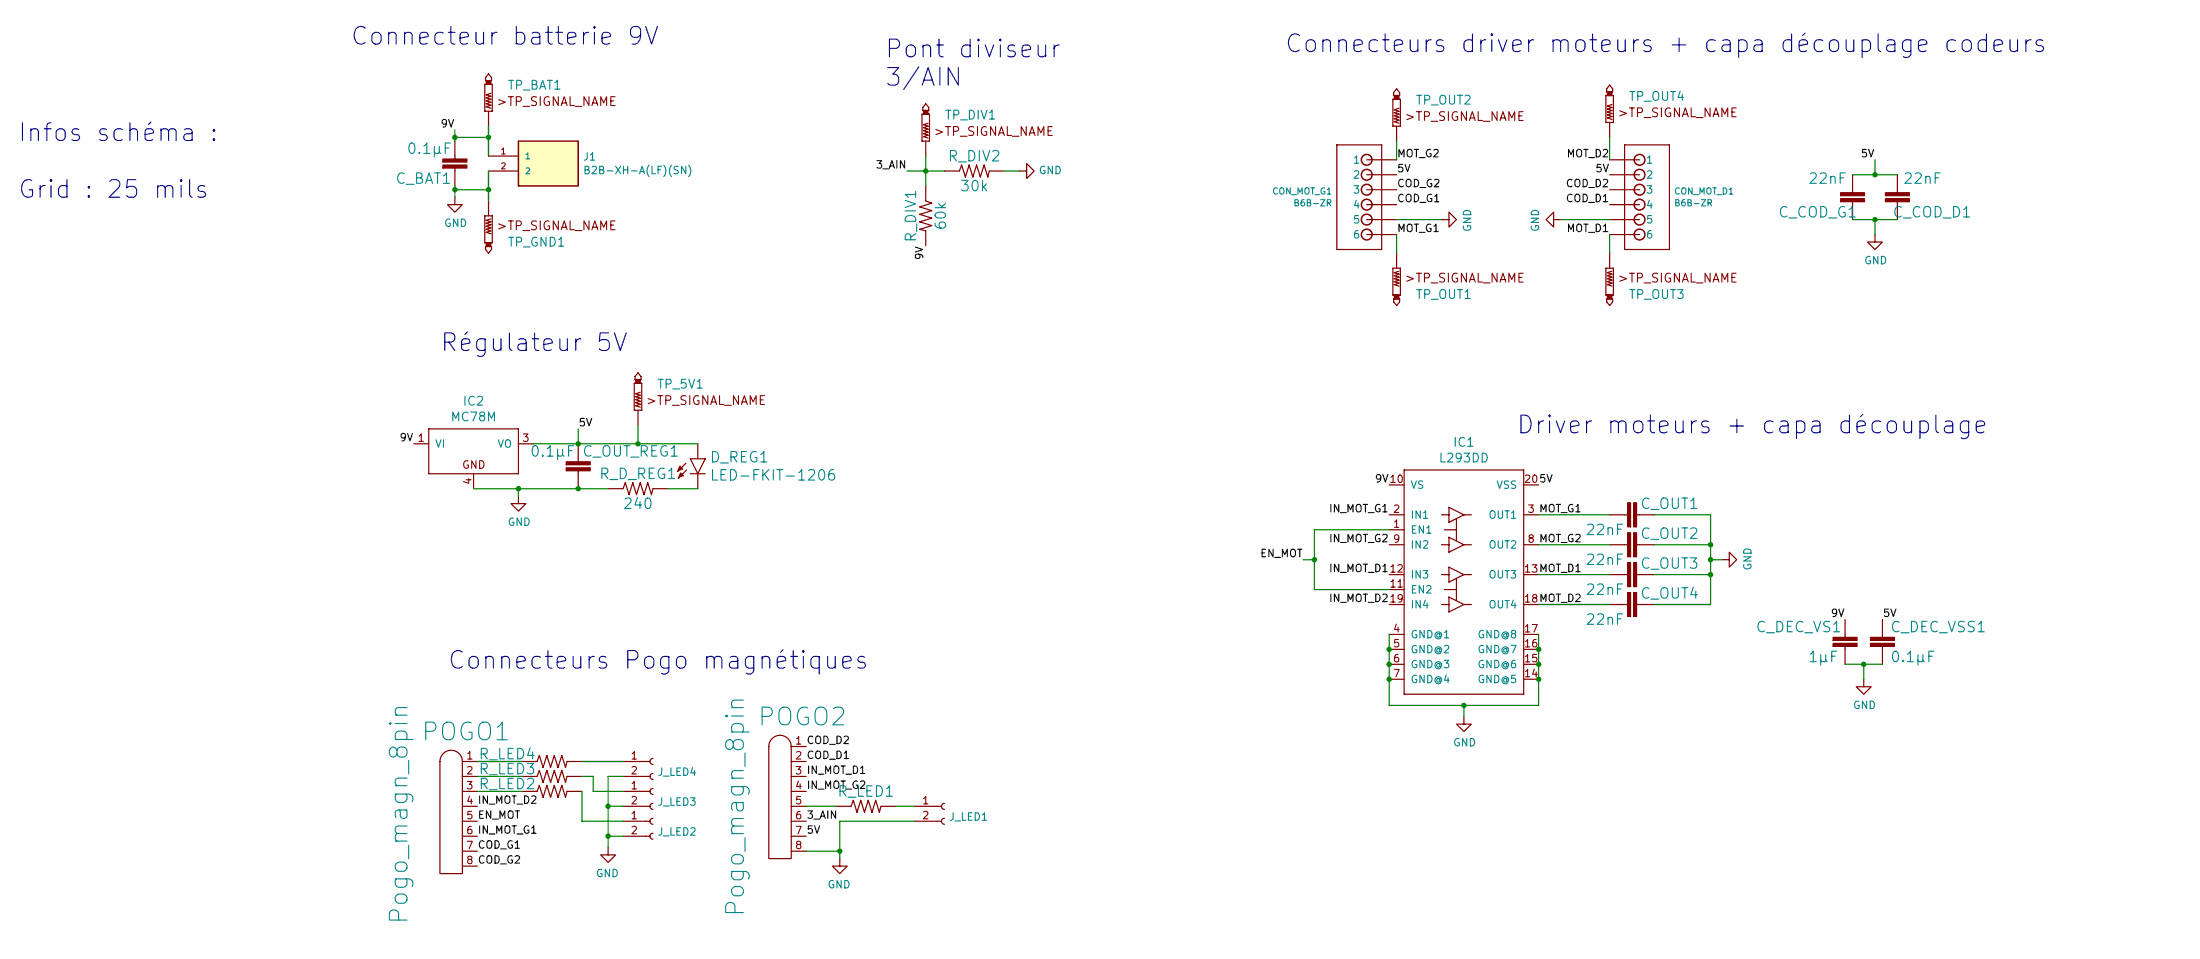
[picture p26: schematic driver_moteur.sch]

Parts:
CON_MOT_D1: B6B-ZR
CON_MOT_G1: B6B-ZR
C_BAT1: 0.1µF; 0603
C_COD_D1: 22nF; 0603
C_COD_G1: 22nF; 0603
C_DEC_VS1: 1µF; 0603
C_DEC_VSS1: 0.1µF; 0603
C_OUT1, C_OUT2, C_OUT3, C_OUT4: 22nF; 0603
C_OUT_REG1: 0.1µF; 0603
D_REG1: LED-FKIT-1206; FKIT-LED-1206
IC1: L293DD; SO20
IC2: MC78M; DPACK_3
J1: B2B-XH-A(LF)(SN); JST_B2B-XH-A(LF)(SN); PARTREV N/A
J_LED1, J_LED2, J_LED3, J_LED4: Conn_01x02_Female; PinHeader_1x02_P2.54mm_Vertical
POGO1, POGO2: Pogo_magn_8pin; CONN_pogopin_8_female
R_DIV1: 60k; 0603
R_DIV2: 30k; 0603
R_D_REG1: 240; 0603
R_LED1, R_LED2, R_LED3, R_LED4: ?; 0603
TP_5V1: PTR1B1,27; B1,27
TP_BAT1: PTR1B1,27; B1,27
TP_DIV1: PTR1B1,27; B1,27
TP_GND1: PTR1B1,27; B1,27
TP_OUT1, TP_OUT2, TP_OUT3, TP_OUT4: PTR1B1,27; B1,27

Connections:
/3_AIN: POGO2.6, R_DIV1.1, R_DIV2.1, TP_DIV1.TP
/5V: CON_MOT_D1.2, CON_MOT_G1.2, C_COD_D1.1, C_COD_G1.1, C_DEC_VSS1.1, C_OUT_REG1.1, D_REG1.A, IC1.20 (VSS), IC2.3 (VO), POGO2.7, TP_5V1.TP
/9V: C_BAT1.1, C_DEC_VS1.1, IC1.10 (VS), IC2.1 (VI), J1.1, R_DIV1.2, TP_BAT1.TP
/COD_D1: CON_MOT_D1.4, POGO2.2
/COD_D2: CON_MOT_D1.3, POGO2.1
/COD_G1: CON_MOT_G1.4, POGO1.7
/COD_G2: CON_MOT_G1.3, POGO1.8
/EN_MOT: IC1.1 (EN1), IC1.11 (EN2), POGO1.5
/IN_MOT_D1: IC1.12 (IN3), POGO2.3
/IN_MOT_D2: IC1.19 (IN4), POGO1.4
/IN_MOT_G1: IC1.2 (IN1), POGO1.6
/IN_MOT_G2: IC1.9 (IN2), POGO2.4
/MOT_D1: CON_MOT_D1.6, C_OUT3.1, IC1.13 (OUT3), TP_OUT3.TP
/MOT_D2: CON_MOT_D1.1, C_OUT4.1, IC1.18 (OUT4), TP_OUT4.TP
/MOT_G1: CON_MOT_G1.6, C_OUT1.1, IC1.3 (OUT1), TP_OUT1.TP
/MOT_G2: CON_MOT_G1.1, C_OUT2.1, IC1.8 (OUT2), TP_OUT2.TP
GND: CON_MOT_D1.5, CON_MOT_G1.5, C_BAT1.2, C_COD_D1.2, C_COD_G1.2, C_DEC_VS1.2, C_DEC_VSS1.2, C_OUT1.2, C_OUT2.2, C_OUT3.2, C_OUT4.2, C_OUT_REG1.2, IC1.4 (GND@1), IC1.5 (GND@2), IC1.6 (GND@3), IC1.7 (GND@4), IC1.14 (GND@5), IC1.15 (GND@6), IC1.16 (GND@7), IC1.17 (GND@8), IC2.4 (GND), J1.2, J_LED1.2, J_LED2.2, J_LED3.2, J_LED4.2, POGO2.8, R_DIV2.2, R_D_REG1.1, TP_GND1.TP
unnamed: D_REG1.C, R_D_REG1.2
unnamed: J_LED1.1, R_LED1.2
unnamed: J_LED2.1, R_LED2.2
unnamed: J_LED3.1, R_LED3.2
unnamed: J_LED4.1, R_LED4.2
unnamed: POGO1.1, R_LED4.1
unnamed: POGO1.2, R_LED3.1
unnamed: POGO1.3, R_LED2.1
unnamed: POGO2.5, R_LED1.1

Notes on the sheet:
Régulateur 5V
Connecteur batterie 9V
Pont diviseur 3/AIN
Connecteurs driver moteurs + capa découplage codeurs
Driver moteurs + capa découplage
Infos schéma : Grid : 25 mils
Connecteurs Pogo magnétiques

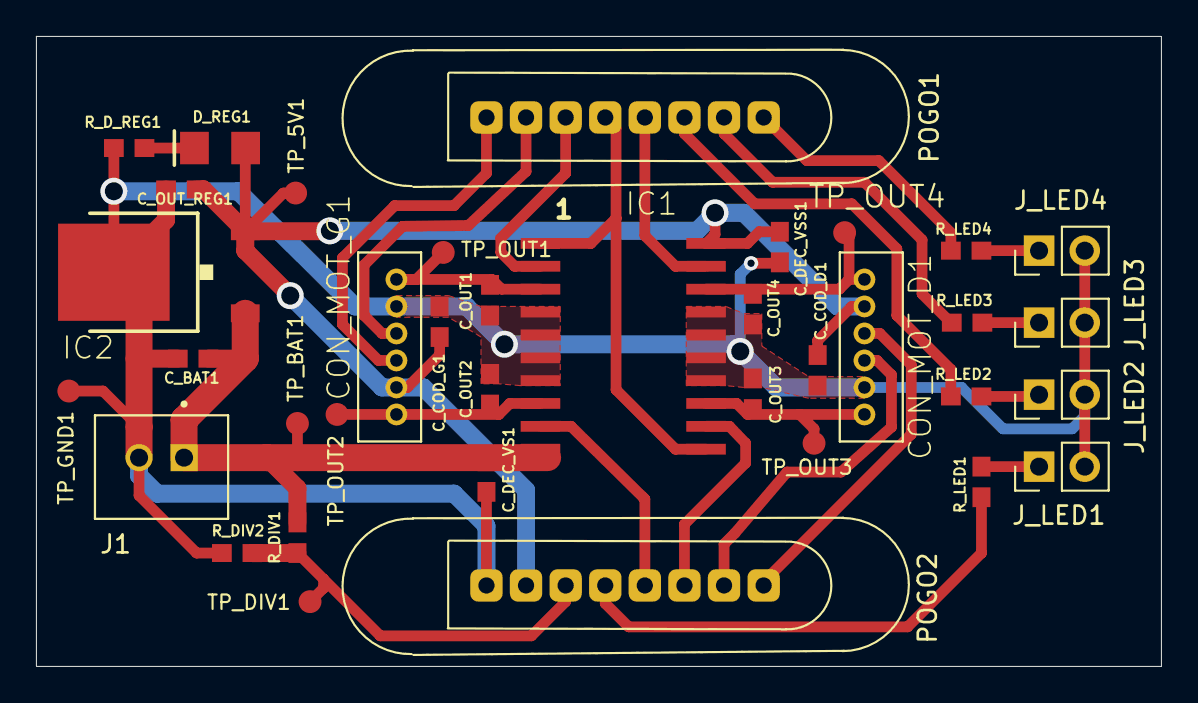
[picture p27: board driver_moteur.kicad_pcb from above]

Board: 2 copper layers, 62.5 x 35.0 mm, 37 parts (0 on the bottom side), 26 nets.

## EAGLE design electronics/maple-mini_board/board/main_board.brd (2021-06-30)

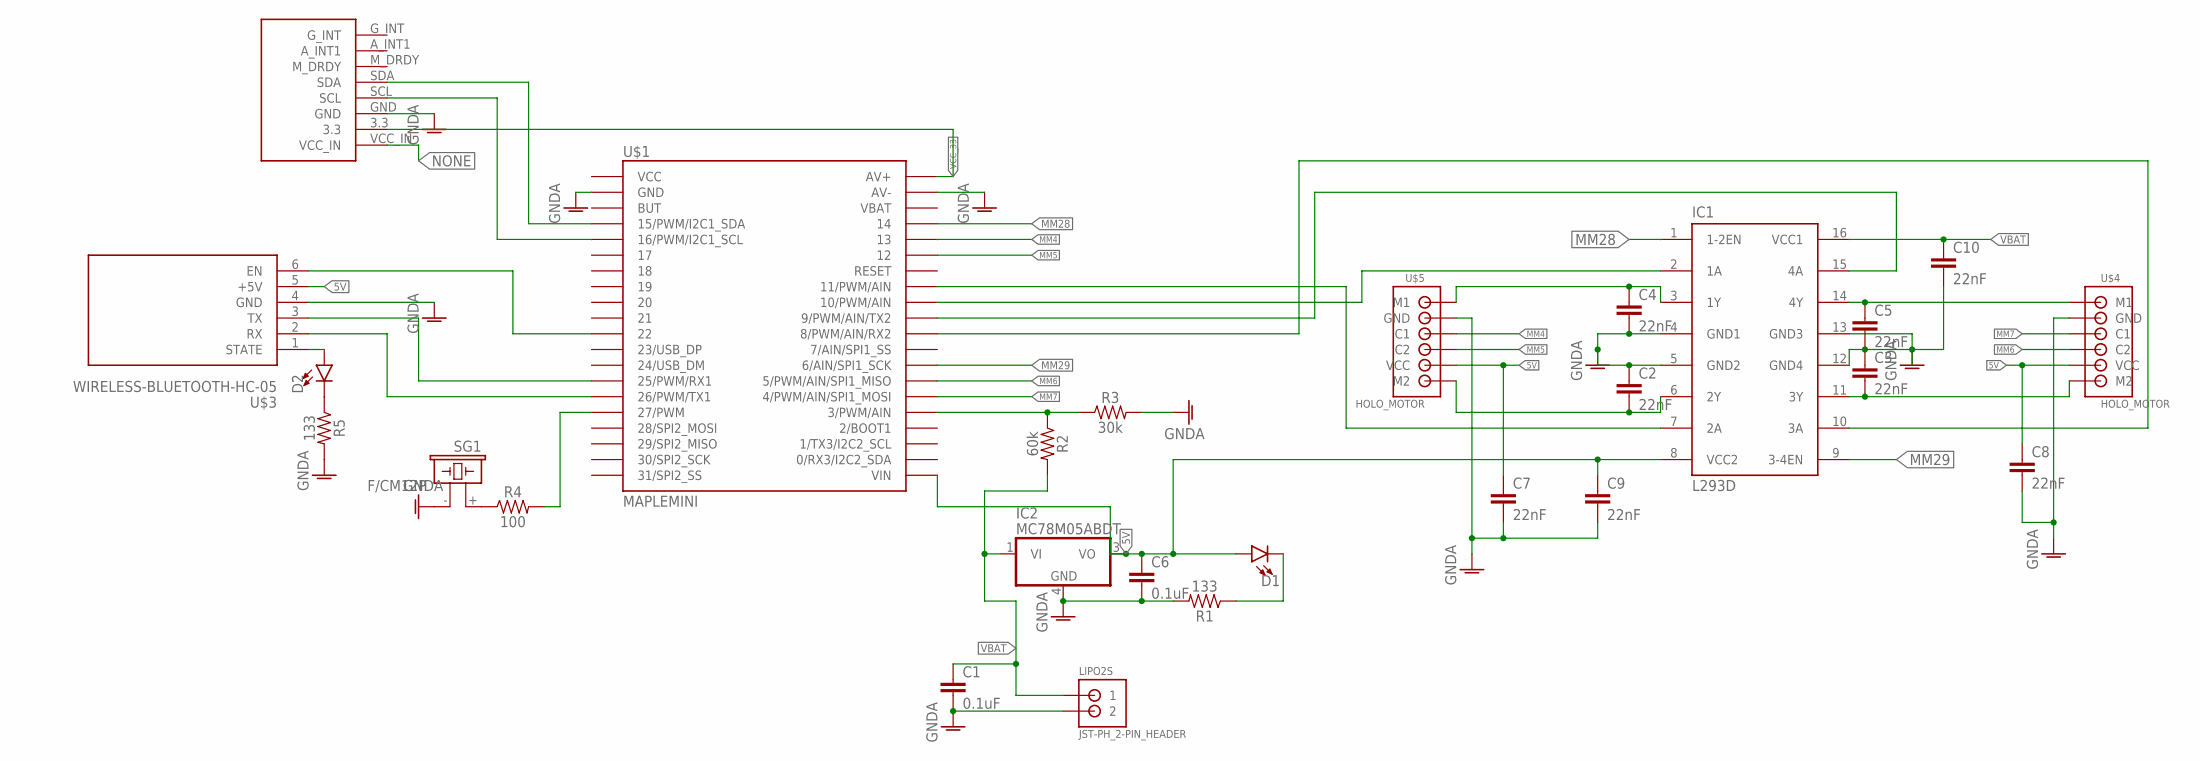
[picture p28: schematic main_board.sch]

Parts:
C1, C6: 0.1uF; 0603
C2, C3, C4, C5, C7, C8, C9, C10: 22nF; 0603
D1, D2: LED-FKIT-1206; FKIT-LED-1206
IC1: L293D; DIL16
IC2: MC78M05ABDT; DPACK_3
LIPO2S: JST-PH_2-PIN_HEADER; JST_B2B-PH_HEADER
R1, R5: 133; 0603
R2: 60k; 0603
R3: 30k; 0603
R4: 100; 0603
SG1: F/CM12P
U$1: MAPLEMINI; 20-DIP
U$3: WIRELESS-BLUETOOTH-HC-05
U$4, U$5: HOLO_MOTOR
U$6: GY-85

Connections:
5V: C6.1, C7.1, C8.1, C9.1, D1.A, IC1.8 (VCC2), IC2.3 (VO), U$1.21 (VIN), U$3.5 (+5V), U$4.5 (VCC), U$5.5 (VCC)
GNDA: C1.2, C2.1, C3.1, C4.2, C5.2, C6.2, C7.2, C8.2, C9.2, C10.2, IC1.4 (GND1), IC1.5 (GND2), IC1.12 (GND4), IC1.13 (GND3), IC2.4 (GND), LIPO2S.P2 (2), R1.2, R3.2, R5.2, SG1.- (2), U$1.2 (GND), U$1.39 (AV-), U$3.4 (GND), U$4.2 (GND), U$5.2 (GND), U$6.GND
MM4: U$1.36 (13), U$5.3 (C1)
MM5: U$1.35 (12), U$5.4 (C2)
MM6: U$1.27 (5/PWM/AIN/SPI1_MISO), U$4.4 (C2)
MM7: U$1.26 (4/PWM/AIN/SPI1_MOSI), U$4.3 (C1)
MM28: IC1.1 (1-2EN), U$1.37 (14)
MM29: IC1.9 (3-4EN), U$1.28 (6/AIN/SPI1_SCK)
unnamed: D1.C, R1.1
unnamed: R4.2, U$1.16 (27/PWM)
unnamed: IC1.10 (3A), U$1.30 (8/PWM/AIN/RX2)
unnamed: U$1.15 (26/PWM/TX1), U$3.2 (RX)
unnamed: U$1.14 (25/PWM/RX1), U$3.3 (TX)
unnamed: U$1.5 (16/PWM/I2C1_SCL), U$6.SCL
unnamed: C5.1, IC1.14 (4Y), U$4.1 (M1)
unnamed: U$1.11 (22), U$3.6 (EN)
unnamed: R2.1, R3.1, U$1.25 (3/PWM/AIN)
unnamed: IC1.7 (2A), U$1.33 (11/PWM/AIN)
unnamed: IC1.2 (1A), U$1.32 (10/PWM/AIN)
unnamed: IC1.15 (4A), U$1.31 (9/PWM/AIN/TX2)
unnamed: U$1.4 (15/PWM/I2C1_SDA), U$6.SDA
unnamed: R4.1, SG1.+ (1)
unnamed: C4.1, IC1.3 (1Y), U$5.1 (M1)
unnamed: C3.2, IC1.11 (3Y), U$4.6 (M2)
unnamed: C2.2, IC1.6 (2Y), U$5.6 (M2)
unnamed: D2.A, U$3.1 (STATE)
unnamed: D2.C, R5.1
NONE: U$6.VCC_IN
VBAT: C1.1, C10.1, IC1.16 (VCC1), IC2.1 (VI), LIPO2S.P1 (1), R2.2
VCC_33: U$1.40 (AV+), U$6.3.3

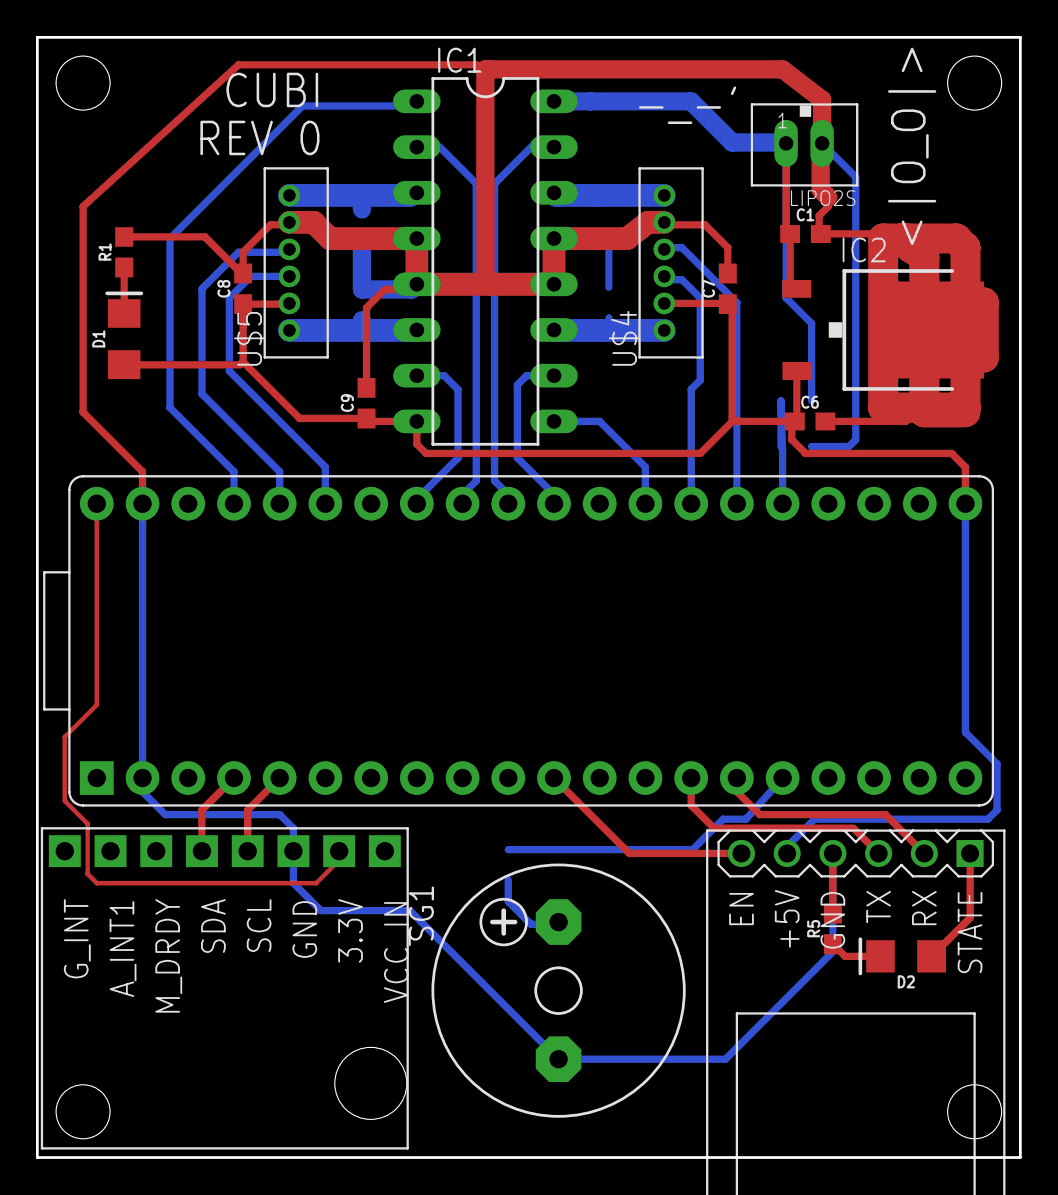
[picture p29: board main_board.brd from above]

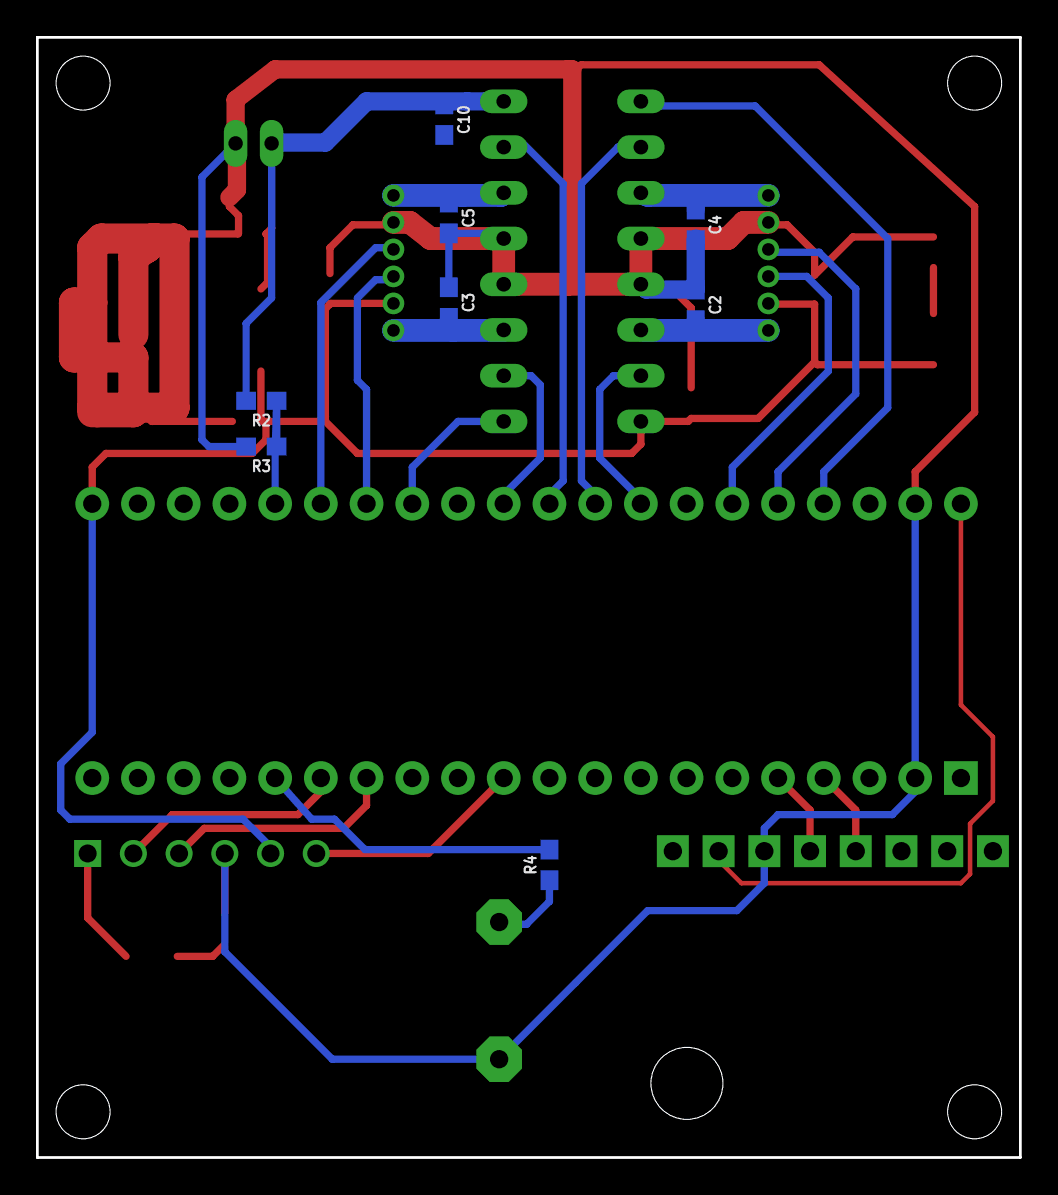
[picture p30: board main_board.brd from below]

Board: 2 copper layers, 54.6 x 62.2 mm, 26 parts (8 on the bottom side), 29 nets.

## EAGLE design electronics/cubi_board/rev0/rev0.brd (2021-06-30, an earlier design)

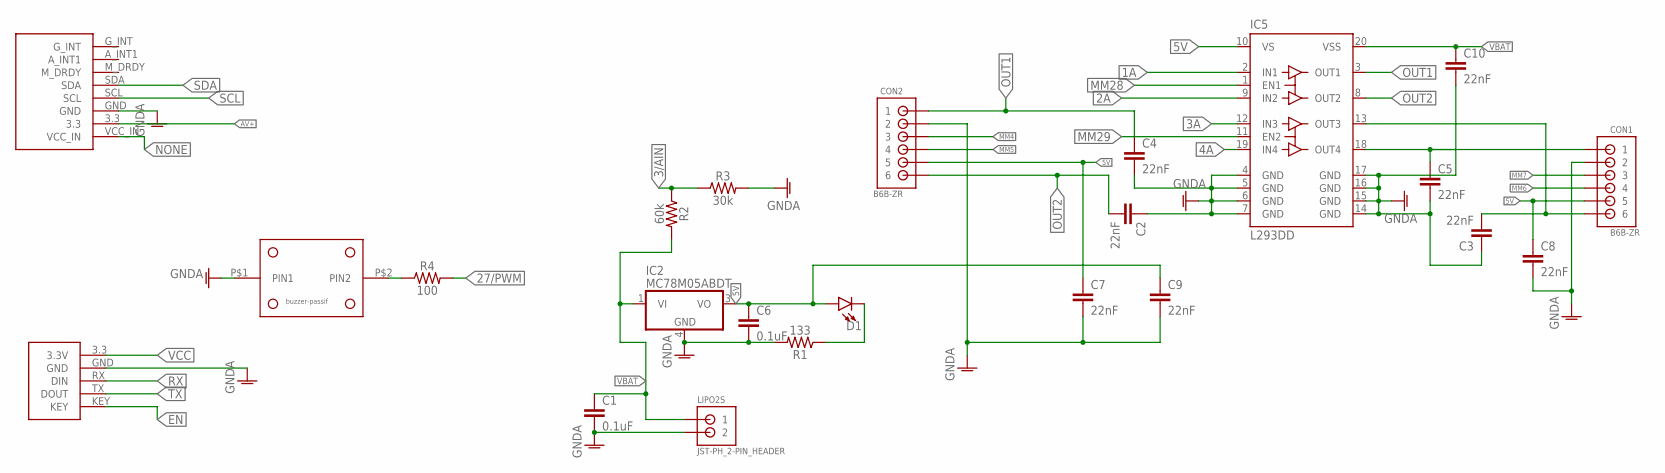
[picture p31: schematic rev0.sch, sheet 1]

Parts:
C1, C6: 0.1uF; 0603
C2, C3, C4, C5, C7, C8, C9, C10: 22nF; 0603
CON1, CON2: B6B-ZR
D1: LED-FKIT-1206; FKIT-LED-1206
IC2: MC78M05ABDT; DPACK_3
IC5: L293DD; SO20
LIPO2S: JST-PH_2-PIN_HEADER; JST_B2B-PH_HEADER
R1: 133; 0603
R2: 60k; 0603
R3: 30k; 0603
R4: 100; 0603
U$1: BUZZER-PASSIF
U$4: HC05; HC-05; FARNELL MODULE HC-05
U$6: GY-85

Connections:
1A: IC5.2 (IN1); also elsewhere on the board
2A: IC5.9 (IN2); also elsewhere on the board
3/AIN: R2.1, R3.1; also elsewhere on the board
3A: IC5.12 (IN3); also elsewhere on the board
4A: IC5.19 (IN4); also elsewhere on the board
5V: C6.1, C7.1, C8.1, C9.1, CON1.5, CON2.5, D1.A, IC2.3 (VO), IC5.10 (VS)
27/PWM: R4.2; also elsewhere on the board
AV+: U$6.3.3; also elsewhere on the board
EN: U$4.KEY; also elsewhere on the board
GNDA: C1.2, C2.1, C3.1, C4.2, C5.2, C6.2, C7.2, C8.2, C9.2, C10.2, CON1.2, CON2.2, IC2.4 (GND), IC5.4 (GND), IC5.5 (GND), IC5.6 (GND), IC5.7 (GND), IC5.14 (GND), IC5.15 (GND), IC5.16 (GND), IC5.17 (GND), LIPO2S.P2 (2), R1.2, R3.2, U$1.P$1 (PIN1), U$4.GND, U$6.GND
MM4: CON2.3; also elsewhere on the board
MM5: CON2.4; also elsewhere on the board
MM6: CON1.4; also elsewhere on the board
MM7: CON1.3; also elsewhere on the board
MM28: IC5.1 (EN1); also elsewhere on the board
MM29: IC5.11 (EN2); also elsewhere on the board
unnamed: D1.C, R1.1
unnamed: R4.1, U$1.P$2 (PIN2)
NONE: U$6.VCC_IN
OUT1: C4.1, CON2.1, IC5.3 (OUT1)
OUT2: C2.2, CON2.6, IC5.8 (OUT2)
OUT3: C3.2, CON1.6, IC5.13 (OUT3)
OUT4: C5.1, CON1.1, IC5.18 (OUT4)
RX: U$4.RX (DIN); also elsewhere on the board
SCL: U$6.SCL; also elsewhere on the board
SDA: U$6.SDA; also elsewhere on the board
TX: U$4.TX (DOUT); also elsewhere on the board
VBAT: C1.1, C10.1, IC2.1 (VI), IC5.20 (VSS), LIPO2S.P1 (1), R2.2; also elsewhere on the board
VCC: U$4.3.3 (3.3V); also elsewhere on the board

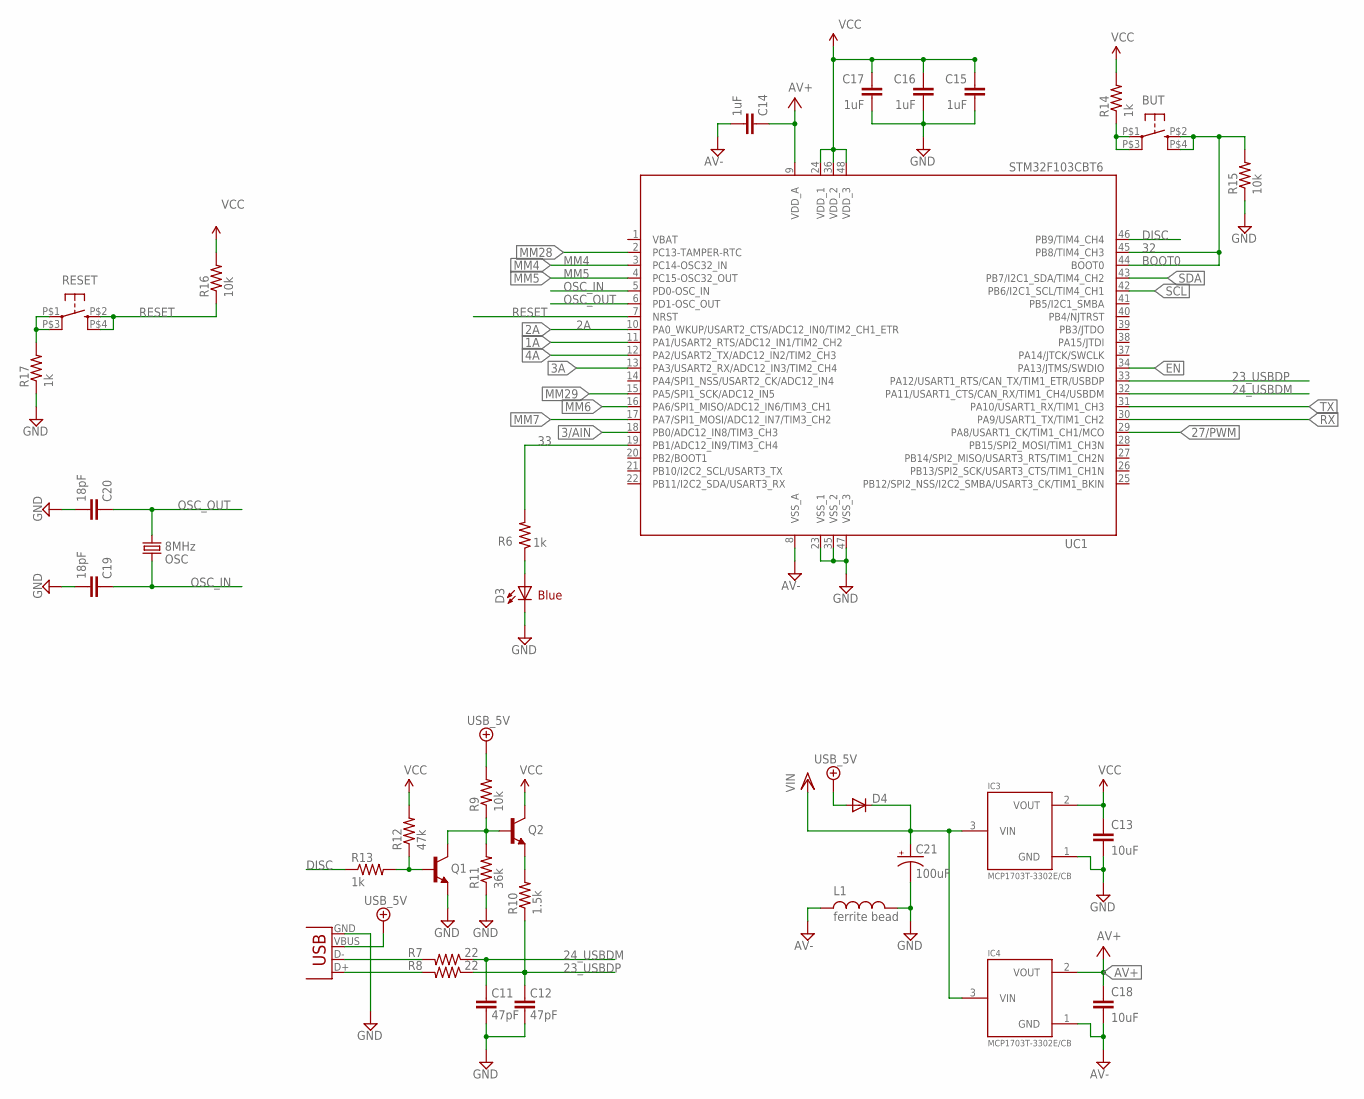
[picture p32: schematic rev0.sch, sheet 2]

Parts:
BUT: KMR211GLFS; PUSHBUTTON-KMR241GLFS
C11, C12: 47pF; C0402
C13, C18: 10uF; 0805
C14, C15, C16, C17: 1uF; C0402
C19, C20: 18pF; C0402
C21: 100uF; EIA3216
D3: Blue; LED-1206
D4: DIODESOD; SOD-323
IC3, IC4: MCP1703T-3302E/CB; SOT23
L1: ferrite bead; 0603
OSC: 8MHz; CRYSTAL-SMD-5X3
Q1, Q2: NPN-BJT; SOT23
R6, R13, R14, R17: 1k; C0402
R7, R8: 22; C0402
R9, R15, R16: 10k; C0402
R10: 1.5k; C0402
R11: 36k; C0402
R12: 47k; C0402
RESET: KMR211GLFS; PUSHBUTTON-KMR241GLFS
UC1: STM32F103CBT6; LQFP48
X1: USB-MINIB

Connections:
1A: UC1.11 (PA1/USART2_RTS/ADC12_IN1/TIM2_CH2); also elsewhere on the board
2A: UC1.10 (PA0_WKUP/USART2_CTS/ADC12_IN0/TIM2_CH1_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); also elsewhere on the board
3/AIN: UC1.18 (PB0/ADC12_IN8/TIM3_CH3); also elsewhere on the board
3A: UC1.13 (PA3/USART2_RX/ADC12_IN3/TIM2_CH4); also elsewhere on the board
4A: UC1.12 (PA2/USART2_TX/ADC12_IN2/TIM2_CH3); also elsewhere on the board
23_USBDP: C12.2, R8.1, R10.1, UC1.33 (PA12/USART1_RTS/CAN_TX/TIM1_ETR/USBDP)
24_USBDM: C11.2, R7.1, UC1.32 (PA11/USART1_CTS/CAN_RX/TIM1_CH4/USBDM)
27/PWM: UC1.29 (PA8/USART1_CK/TIM1_CH1/MCO); also elsewhere on the board
32: BUT.P$2 (2), BUT.P$4 (4), R15.2, UC1.44 (BOOT0), UC1.45 (PB8/TIM4_CH3)
33: R6.2, UC1.19 (PB1/ADC12_IN9/TIM3_CH4)
+5V/2: D4.2 (A), R9.2, X1.VBUS
AV+: C14.1, C18.1, IC4.2 (VOUT), UC1.9 (VDD_A); also elsewhere on the board
AV-: C14.2, C18.2, IC4.1 (GND), L1.1, UC1.8 (VSS_A)
DGND: C11.1, C12.1, C13.2, C15.2, C16.2, C17.2, C19.2, C20.2, C21.C (-), D3.C, IC3.1 (GND), L1.2, Q1.2 (E), R11.1, R15.1, R17.1, UC1.23 (VSS_1), UC1.35 (VSS_2), UC1.47 (VSS_3), X1.GND
DISC: R13.1, UC1.46 (PB9/TIM4_CH4)
EN: UC1.34 (PA13/JTMS/SWDIO); also elsewhere on the board
MM4: UC1.3 (PC14-OSC32_IN); also elsewhere on the board
MM5: UC1.4 (PC15-OSC32_OUT); also elsewhere on the board
MM6: UC1.16 (PA6/SPI1_MISO/ADC12_IN6/TIM3_CH1); also elsewhere on the board
MM7: UC1.17 (PA7/SPI1_MOSI/ADC12_IN7/TIM3_CH2); also elsewhere on the board
MM28: UC1.2 (PC13-TAMPER-RTC); also elsewhere on the board
MM29: UC1.15 (PA5/SPI1_SCK/ADC12_IN5); also elsewhere on the board
unnamed: BUT.P$1 (1), BUT.P$3 (3), R14.1
unnamed: R17.2, RESET.P$1 (1), RESET.P$3 (3)
unnamed: D3.A, R6.1
unnamed: Q2.2 (E), R10.2
unnamed: R7.2, X1.D-
unnamed: R8.2, X1.D+
unnamed: Q1.3 (C), Q2.1 (B), R9.1, R11.2
unnamed: Q1.1 (B), R12.1, R13.2
OSC_IN: C19.1, OSC.3 (2), UC1.5 (PD0-OSC_IN)
OSC_OUT: C20.1, OSC.1, UC1.6 (PD1-OSC_OUT)
RESET: R16.1, RESET.P$2 (2), RESET.P$4 (4), UC1.7 (NRST)
RX: UC1.30 (PA9/USART1_TX/TIM1_CH2); also elsewhere on the board
SCL: UC1.42 (PB6/I2C1_SCL/TIM4_CH1); also elsewhere on the board
SDA: UC1.43 (PB7/I2C1_SDA/TIM4_CH2); also elsewhere on the board
TX: UC1.31 (PA10/USART1_RX/TIM1_CH3); also elsewhere on the board
VBAT: UC1.1 (VBAT); also elsewhere on the board
VCC: C13.1, C15.1, C16.1, C17.1, IC3.2 (VOUT), Q2.3 (C), R12.2, R14.2, R16.2, UC1.24 (VDD_1), UC1.36 (VDD_2), UC1.48 (VDD_3); also elsewhere on the board
VIN: C21.A (+), D4.1 (C), IC3.3 (VIN), IC4.3 (VIN)

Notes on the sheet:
BOOT0
Blue

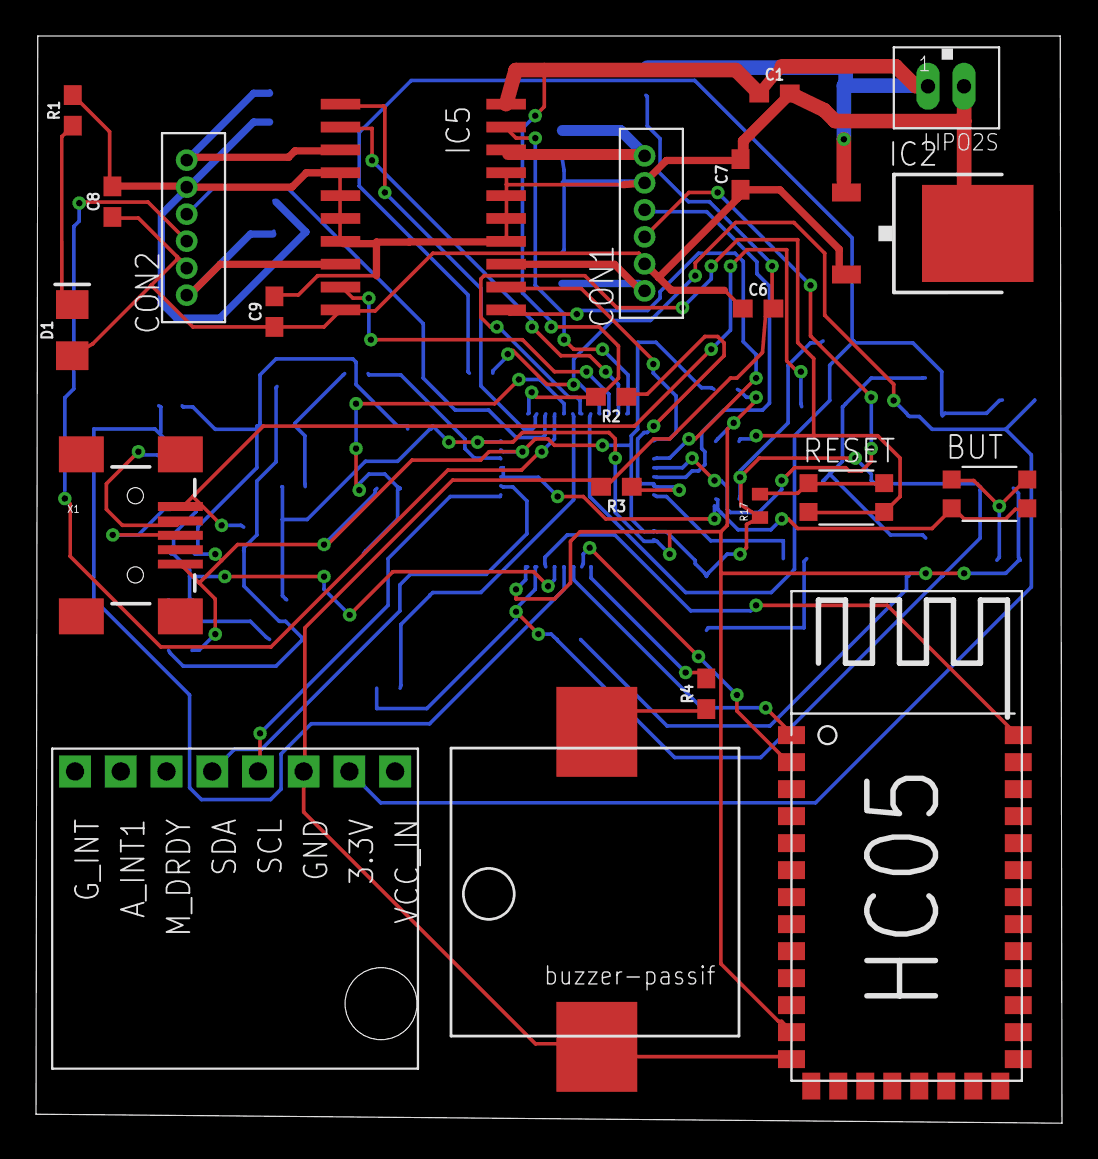
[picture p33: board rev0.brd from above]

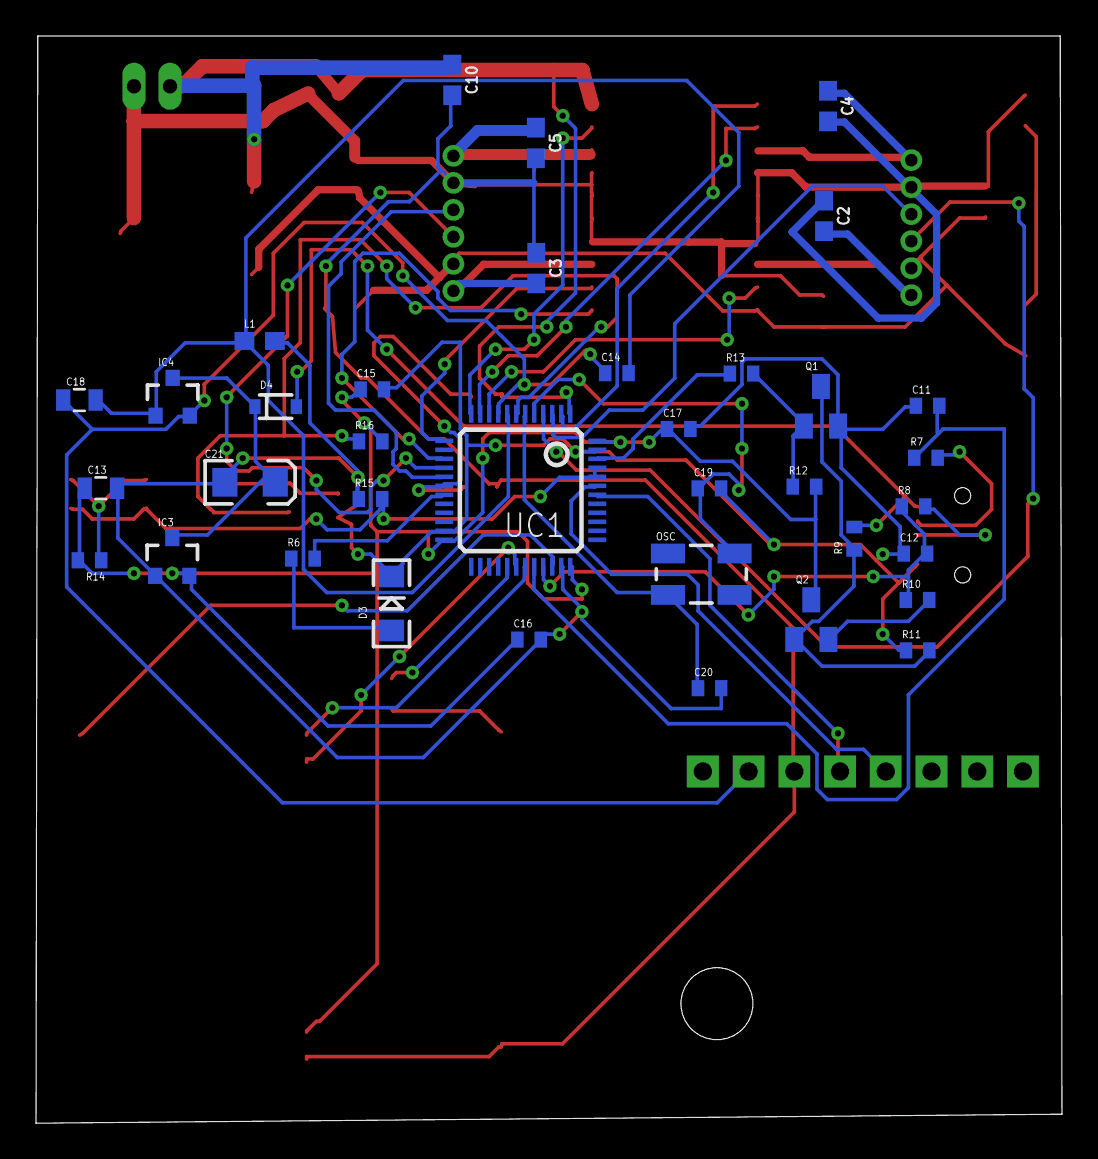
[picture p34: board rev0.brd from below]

Board: 2 copper layers, 57.0 x 60.4 mm, 58 parts (36 on the bottom side), 48 nets.

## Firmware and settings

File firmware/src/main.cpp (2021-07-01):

#include <stdlib.h>
#include <wirish/wirish.h>
#include <terminal.h>
#include <libmaple/adc.h>
#include <libmaple/timer.h>
#include <main.h>
#include "dc.h"
#include "buzzer.h"
#include "voltage.h"
#include "bt.h"
#include "model.h"
#include "imu.h"
#include "helpers.h"

#define NOSOUND 0
#define BAUDRATE 115200

// Without weights :
// #define CART_KP 1000
// #define CART_KI 10000
// #define CART_KD 40

// With weights
// #define CART_KP 2000
// #define CART_KI 25000
// #define CART_KD 60

#define CART_KP 4000
#define CART_KI 50000
#define CART_KD 100



#define X_KP 0 //2
#define X_KI 0 //10

/*
  Timer2 controls the pwms 8, 9, 10 and 11
 */

int my_atoi(char *p, bool *success);
void default_cart_pole();

bool isUSB = false;
bool isUSBForEver = true;
long counter = 0;
unsigned int hardwareCounter = 0;
bool readyToUpdateHardware = false;
bool led_state = false;

static float cart_kp = CART_KP;
static float cart_ki = CART_KI;
static float cart_kd = CART_KD;
static float cart_i_acc = 0;
static float cart_err = 0;
static float cart_last_err = 0;
static float cart_extra_rotation = 0;
static float adapted_cartgoal = 0;

static float cart_x_kp = X_KP;
static float cart_x_ki = X_KI;
static float cart_x_i_acc = 0;
static float cart_x_err = 0;

// Timming
static uint32 dt = 0;
static uint32 dt_ms = 0;
static uint32 dt_cart = 0;
static uint32 last_dt_cart = 0;
static uint32 time_micros = 0;
static uint32 old_time_micros = 0;
static uint32 time_ms = 0;
static uint32 old_time_ms = 0;
static uint32 half_max = (1 << 31);

TERMINAL_COMMAND(freq, "Returns the last measure of dt (the period of the main loop in micros)")
{
    terminal_io()->print(micros());
    terminal_io()->print(" = micros(), ");
    terminal_io()->print(millis());
    terminal_io()->print(" = millis(), dt = ");
    terminal_io()->print(dt);
    terminal_io()->print(" us, dt = ");
    terminal_io()->print(dt_ms);
    terminal_io()->print(" ms, freq = ");
    terminal_io()->print(1000000.0 / dt);
    terminal_io()->print(" Hz, dt_cart = ");
    terminal_io()->print(last_dt_cart);
    terminal_io()->print(" us, cart_freq = ");
    if (last_dt_cart != 0)
    {
        terminal_io()->print(1000000.0 / last_dt_cart);
        terminal_io()->println(" Hz");
    }
    else
    {
        terminal_io()->println(" I ain't no dividing by no zero");
    }
}

TERMINAL_COMMAND(carterr, "Debug function")
{
    terminal_io()->print("cart_err = ");
    terminal_io()->print(cart_err);
    terminal_io()->print(", cart_last_err = ");
    terminal_io()->println(cart_last_err);
}

TERMINAL_COMMAND(pwm, "[usage] pwm pwm_value1 pwm_value2")
{
    if (argc == 2)
    {
        bool success = false;
        int pwm1 = my_atoi(argv[0], &success);
        int pwm2 = my_atoi(argv[1], &success);
        _limit(&pwm1, MAX_PWM);
        _limit(&pwm2, MAX_PWM);
        dc_motor *motors = get_motors();
        motors[0].command = pwm1;
        motors[1].command = pwm2;
        terminal_io()->print("Setting pwms ");
        terminal_io()->print(pwm1);
        terminal_io()->print(" and ");
        terminal_io()->println(pwm2);
    }
    else
    {
        terminal_io()->println("[usage] pwm pwm_value1 pwm_value2");
    }
}

TERMINAL_COMMAND(rc, "Go to bluetooth serial mode")
{
    // Terminal management
    Serial1.begin(BAUDRATE);
    terminal_init(&Serial1);
    isUSB = false;
    isUSBForEver = false;
}
TERMINAL_COMMAND(usb, "Go to USB serial mode")
{
    // Terminal management
    isUSB = true;
    terminal_init(&SerialUSB);
    isUSBForEver = true;
}

TERMINAL_PARAMETER_BOOL(cartpole, "activates the cartpole mode", false);
TERMINAL_PARAMETER_FLOAT(cartgoal, "Angle goal for the inverted pendulum", 1.607);
TERMINAL_PARAMETER_FLOAT(criticangle, "Max angle we're allowed to aim around the vertical point to control the robot in rad", 0.005);

TERMINAL_COMMAND(cart, "goal(rads) [kp] [ki] [kd] [rotation]")
{
    if (argc >= 1)
    {
        cartpole = true;
        cartgoal = atof(argv[0]);
        // Resetting the accumulator
        cart_i_acc = 0;
    }
    if (argc >= 2)
    {
        cart_kp = atof(argv[1]);
        cart_ki = 0;
        cart_kd = 0;
    }
    if (argc >= 3)
    {
        cart_ki = atof(argv[2]);
        cart_kd = 0;
    }
    if (argc >= 4)
    {
        cart_kd = atof(argv[3]);
    }
    if (argc >= 5)
    {
        cart_extra_rotation = atof(argv[3]);
    }
}

TERMINAL_COMMAND(a, "debug")
{
    terminal_io()->println(adapted_cartgoal);
}

TERMINAL_COMMAND(c, "cartpole pid values: kp ki kd [rotation]")
{
    if (argc >= 3)
    {
        // Resetting the accumulator
        cart_i_acc = 0;
        cart_kp = atof(argv[0]);
        cart_ki = atof(argv[1]);
        cart_kd = atof(argv[2]);
    }
    if (argc >= 4)
    {
        cart_extra_rotation = atof(argv[3]);
    }
}

TERMINAL_COMMAND(d, "cartpole X pi values: kp ki")
{
    if (argc >= 2)
    {
        // Resetting the accumulator
        cart_x_i_acc = 0;
        cart_x_kp = atof(argv[0]);
        cart_x_ki = atof(argv[1]);
    }
}



void default_cart_pole() {
    // Resetting the accumulator
    cart_i_acc = 0;
    cartpole = 1;
    model_reset();
    cart_kp = CART_KP;
    cart_ki = CART_KI;
    cart_kd = CART_KD;
    cart_x_kp = X_KP;
    cart_x_ki = X_KI;

    get_model()->mode = MODE_SPEED_CONTROL;
}

TERMINAL_COMMAND(cd, "op command that sets the robot in inverted pendulum mode with default values")
{
    default_cart_pole();
}

void setup()
{
    // Wirish board specific init
    disableDebugPorts();

    pinMode(BOARD_LED_PIN, OUTPUT);
    pinMode(BOARD_BUTTON_PIN, INPUT);

    buzzer_init();
    if (!NOSOUND)
    {
        buzzer_play(MELODY_BEGIN);
    }
    // Initializing IMU
    imu_init();

    model_init();
    motor_init();
    voltage_init();
    bt_init();

    // Terminal management
    Serial1.begin(BAUDRATE);
    // The HC05 is connected to Serial1
    terminal_init(&Serial1);
    digitalWrite(BOARD_LED_PIN, HIGH);
    digitalWrite(PWM12_ENABLE, HIGH);
    old_time_micros = micros();
    old_time_ms = millis();
}

void loop()
{
    counter++;
    time_micros = micros();
    time_ms = millis();
    dt = time_micros - old_time_micros;
    dt_ms = time_ms - old_time_ms;


    if (dt > half_max)
    {
        // It probably means that the value reached its maximum and reseted
        uint32 max_value = 0;
        max_value = ~(max_value);
        dt = time_micros + (max_value - old_time_micros);
    }
    old_time_micros = time_micros;
    old_time_ms = time_ms;

    if (counter < 500)
    {
        digitalWrite(BOARD_LED_PIN, LOW);
    }
    else if (counter >= 500 && counter < 1000)
    {
        digitalWrite(BOARD_LED_PIN, HIGH);
    }
    else
    {
        counter = 0;
    }

    if (counter % 100 == 0)
    {
        // By default, the Serial used is the Bluetooth, except if a the SerialUSB is being written.
        // The isUSBForEver flag is used to persist in USB or in bluetooth, when asked through the terminal commands (rc/usb)
        if (SerialUSB.available() && !isUSB && isUSBForEver)
        {
            isUSB = true;
            terminal_init(&SerialUSB);
        }
    }

    if (digitalRead(BOARD_BUTTON_PIN))
    {
        default_cart_pole();
    }
    
    // Ticking IMU
    imu_tick();

    dt_cart = dt_cart + dt;

    if (cartpole && imu_is_checked)
    {
        imu_is_checked = false;
        cart_last_err = cart_err;

        // The angle goal is very slighlty modified with a PI controller so the X position of the robot (integrated through odometry) stays at what we want it to be
        cart_x_err = get_model()->x;

        cart_x_i_acc = cart_x_i_acc + cart_x_ki * cart_x_err * dt_cart / 1000000.0;

        _limit(&cart_x_i_acc, criticangle);

        float temp_sum = (cart_x_kp * cart_x_err + cart_x_i_acc);

        _limit(&temp_sum, criticangle);

        adapted_cartgoal = cartgoal + temp_sum;

        if (cart_x_kp == 0 && cart_x_ki == 0)
        {
            adapted_cartgoal = cartgoal;
        }
        cart_err = smooth_pitch - adapted_cartgoal;
        cart_i_acc = cart_i_acc + cart_ki * cart_err * dt_cart / 1000000.0;
        _limit(&cart_i_acc, MAX_PWM);
        // Putting minus signs was too exhausting.
        int speed = (int)(cart_kp * (cart_err) + cart_i_acc + cart_kd * (cart_err - cart_last_err) * 1000000 / dt_cart) * (-1);
        _limit(&speed, MAX_PWM);

        dc_motor *motors = get_motors();
        motors[0].speed_target = -speed + cart_extra_rotation;
        motors[1].speed_target = -speed - cart_extra_rotation;
        last_dt_cart = dt_cart;
        dt_cart = 0;
    }

    buzzer_tick();
    voltage_tick();
    terminal_tick();
    model_tick();
    dc_tick();

}

int my_atoi(char *p, bool *success)
{
    int k = 0;
    int sign = 1;
    if (*p == '-')
    {
        sign = -1;
        p++;
    }
    while (*p != '\0')
    {
        int value = *p - '0';
        if (value >= 0 && value <= 9)
        {
            k = k * 10 + value;
            p++;
        }
        else
        {
            *success = false;
            return 0;
        }
    }
    *success = true;
    return k * sign;
}

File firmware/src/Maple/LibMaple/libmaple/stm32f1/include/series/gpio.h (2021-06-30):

/******************************************************************************
 * The MIT License
 *
 * Copyright (c) 2010 Perry Hung.
 * Copyright (c) 2011, 2012 LeafLabs, LLC.
 *
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
 * THE SOFTWARE IS PROVIDED "AS IS", WITHOUT WARRANTY OF ANY KIND,
 * EXPRESS OR IMPLIED, INCLUDING BUT NOT LIMITED TO THE WARRANTIES OF
 * MERCHANTABILITY, FITNESS FOR A PARTICULAR PURPOSE AND
 * NONINFRINGEMENT. IN NO EVENT SHALL THE AUTHORS OR COPYRIGHT HOLDERS
 * BE LIABLE FOR ANY CLAIM, DAMAGES OR OTHER LIABILITY, WHETHER IN AN
 * ACTION OF CONTRACT, TORT OR OTHERWISE, ARISING FROM, OUT OF OR IN
 * CONNECTION WITH THE SOFTWARE OR THE USE OR OTHER DEALINGS IN THE
 * SOFTWARE.
*****************************************************************************/

/**
 * @file libmaple/stm32f1/include/series/gpio.h
 * @brief STM32F1 GPIO and AFIO support.
 * General purpose I/O (GPIO) and Alternate Function I/O (AFIO).
 */

#ifndef _LIBMAPLE_STM32F1_GPIO_H_
#define _LIBMAPLE_STM32F1_GPIO_H_

#ifdef __cplusplus
extern "C"{
#endif

#include <libmaple/stm32.h>
#include <libmaple/libmaple_types.h>
#include <libmaple/exti.h>

/*
 * GPIO register maps and devices
 */

/** GPIO register map type */
typedef struct gpio_reg_map {
    __io uint32 CRL;      /**< Port configuration register low */
    __io uint32 CRH;      /**< Port configuration register high */
    __io uint32 IDR;      /**< Port input data register */
    __io uint32 ODR;      /**< Port output data register */
    __io uint32 BSRR;     /**< Port bit set/reset register */
    __io uint32 BRR;      /**< Port bit reset register */
    __io uint32 LCKR;     /**< Port configuration lock register */
} gpio_reg_map;

struct gpio_dev;
extern struct gpio_dev gpioa;
extern struct gpio_dev* const GPIOA;
extern struct gpio_dev gpiob;
extern struct gpio_dev* const GPIOB;
extern struct gpio_dev gpioc;
extern struct gpio_dev* const GPIOC;
extern struct gpio_dev gpiod;
extern struct gpio_dev* const GPIOD;
#ifdef STM32_HIGH_DENSITY
extern struct gpio_dev gpioe;
extern struct gpio_dev* const GPIOE;
extern struct gpio_dev gpiof;
extern struct gpio_dev* const GPIOF;
extern struct gpio_dev gpiog;
extern struct gpio_dev* const GPIOG;
#endif

/** GPIO port A register map base pointer */
#define GPIOA_BASE                      ((struct gpio_reg_map*)0x40010800)
/** GPIO port B register map base pointer */
#define GPIOB_BASE                      ((struct gpio_reg_map*)0x40010C00)
/** GPIO port C register map base pointer */
#define GPIOC_BASE                      ((struct gpio_reg_map*)0x40011000)
/** GPIO port D register map base pointer */
#define GPIOD_BASE                      ((struct gpio_reg_map*)0x40011400)
/** GPIO port E register map base pointer */
#define GPIOE_BASE                      ((struct gpio_reg_map*)0x40011800)
/** GPIO port F register map base pointer */
#define GPIOF_BASE                      ((struct gpio_reg_map*)0x40011C00)
/** GPIO port G register map base pointer */
#define GPIOG_BASE                      ((struct gpio_reg_map*)0x40012000)

/*
 * GPIO register bit definitions
 */

/* Control registers, low and high */

#define GPIO_CR_CNF                     (0x3 << 2)
#define GPIO_CR_CNF_INPUT_ANALOG        (0x0 << 2)
#define GPIO_CR_CNF_INPUT_FLOATING      (0x1 << 2)
#define GPIO_CR_CNF_INPUT_PU_PD         (0x2 << 2)
#define GPIO_CR_CNF_OUTPUT_PP           (0x0 << 2)
#define GPIO_CR_CNF_OUTPUT_OD           (0x1 << 2)
#define GPIO_CR_CNF_AF_OUTPUT_PP        (0x2 << 2)
#define GPIO_CR_CNF_AF_OUTPUT_OD        (0x3 << 2)
#define GPIO_CR_MODE                    0x3
#define GPIO_CR_MODE_INPUT              0x0
#define GPIO_CR_MODE_OUTPUT_10MHZ       0x1
#define GPIO_CR_MODE_OUTPUT_2MHZ        0x2
#define GPIO_CR_MODE_OUTPUT_50MHZ       0x3

/**
 * @brief GPIO pin modes.
 *
 * These only allow for 50MHZ max output speeds; if you want slower,
 * use direct register access.
 */
typedef enum gpio_pin_mode {
    /** Output push-pull. */
    GPIO_OUTPUT_PP      = GPIO_CR_CNF_OUTPUT_PP | GPIO_CR_MODE_OUTPUT_50MHZ,
    /** Output open-drain. */
    GPIO_OUTPUT_OD      = GPIO_CR_CNF_OUTPUT_OD | GPIO_CR_MODE_OUTPUT_50MHZ,
    /** Alternate function output push-pull. */
    GPIO_AF_OUTPUT_PP   = GPIO_CR_CNF_AF_OUTPUT_PP | GPIO_CR_MODE_OUTPUT_50MHZ,
    /** Alternate function output open drain. */
    GPIO_AF_OUTPUT_OD   = GPIO_CR_CNF_AF_OUTPUT_OD | GPIO_CR_MODE_OUTPUT_50MHZ,
    /** Analog input. */
    GPIO_INPUT_ANALOG   = GPIO_CR_CNF_INPUT_ANALOG | GPIO_CR_MODE_INPUT,
    /** Input floating. */
    GPIO_INPUT_FLOATING = GPIO_CR_CNF_INPUT_FLOATING | GPIO_CR_MODE_INPUT,
    /** Input pull-down. */
    GPIO_INPUT_PD       = GPIO_CR_CNF_INPUT_PU_PD | GPIO_CR_MODE_INPUT,
    /** Input pull-up. */
    GPIO_INPUT_PU, /* (treated a special case, for ODR twiddling) */
} gpio_pin_mode;

/* Hacks for F2: */
#define GPIO_MODE_ANALOG GPIO_INPUT_ANALOG
#define GPIO_MODE_OUTPUT GPIO_OUTPUT_PP

/*
 * AFIO register map
 */
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

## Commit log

2021-06-30 Initial files
    [ANSI (in).dwg, ANSI (in).idw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]
2021-06-30 Adding Maple library
    [flash_0.3.cfg, flash_0.4.cfg]
2021-06-30 Adding current CUBI_BOX layout
2021-06-30 Move electronics
    [.GBL, .GBS, .GTL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]
2021-06-30 Update electronics & mechanics
    [ANSI (in).dwg, ANSI (in).idw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]
2021-07-01 change src
    [flash_0.3.cfg, flash_0.4.cfg]
2021-07-09 Correction README du driver moteur, partie elec

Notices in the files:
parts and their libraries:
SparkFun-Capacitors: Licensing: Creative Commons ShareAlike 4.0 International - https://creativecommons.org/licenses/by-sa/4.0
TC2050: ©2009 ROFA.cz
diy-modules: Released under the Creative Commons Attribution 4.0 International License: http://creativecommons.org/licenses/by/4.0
